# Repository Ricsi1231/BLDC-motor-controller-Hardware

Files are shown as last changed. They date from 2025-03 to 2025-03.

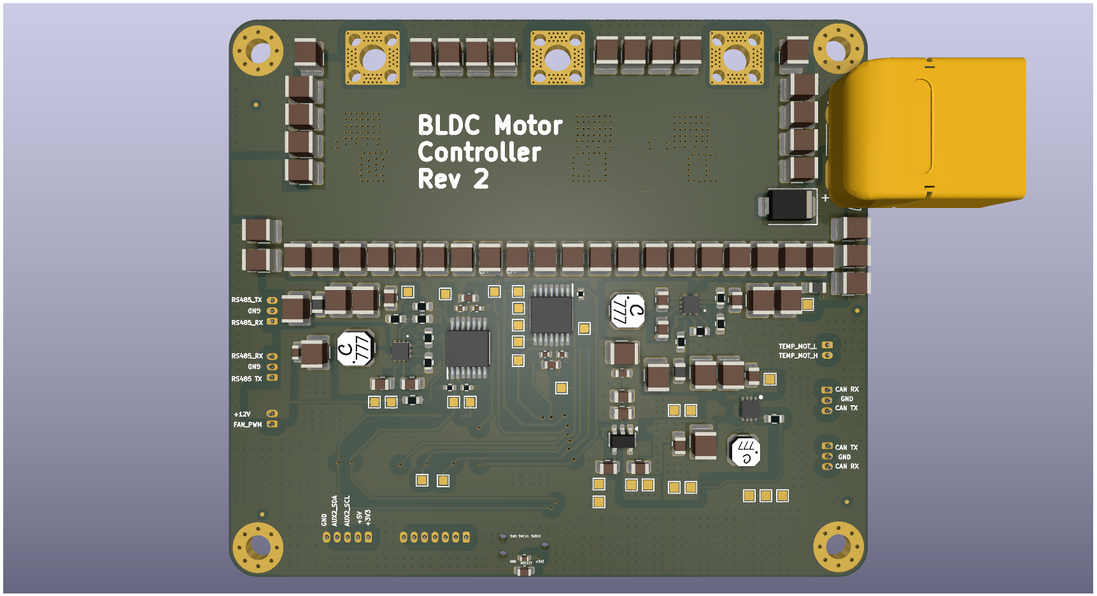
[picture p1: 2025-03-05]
BLDC motor controller/3D/BLDC motor controller - BOTTOM.png

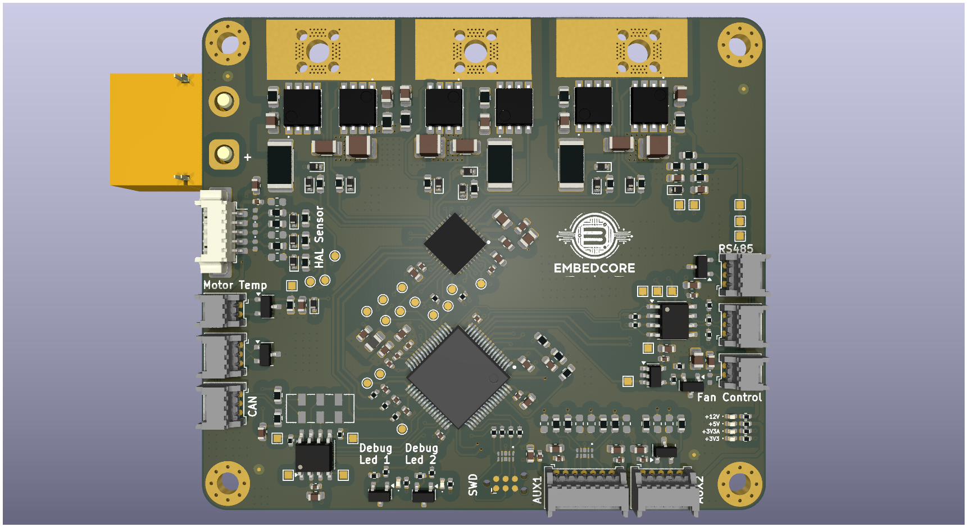
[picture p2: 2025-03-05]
BLDC motor controller/3D/BLDC motor controller - TOP.png

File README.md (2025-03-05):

## EmbedCore - BLDC Motor Controller

EmbedCore motor controller is a high-power brushless motor controller. It was specifically designed to be integrated in Autonomus Mobile Robot wheel actuators. Motor controller can be intagreted to other applications.
BLDC Motor Controller is also my final thesis work at Subotica Tech - College of Applied Sciences.

***

## SPECIFICATIONS

| Parameter | EmbedCore BLDC Controller V1.0 | 
| --- | --- |
| Voltage Input | 12-44V |
| Peak Electrical Power | TBD |
| Mass | TBD |
| Peak Phase Current | 100A |
| Communication | 5Mbps CAN-FD & RS485 |
| Cooling | 12V Fan |
| Positioning | 2x Onboard 14-bit Encoders |
| Control rate | 15-30kHz |
| PWM Switching Rate | 15-60kHz |
| MCU | STM32G474 |
| Dimensions | 67 x 76.5mm |

***

## DIRECTORY STRUCTURE

```
BLDC motor controller
├── 3D                             # 3D render pictures of the board
├── Datasheets                     # Main component datasheets
├── Specification                  # Specification description about the project
├── Documentation
│   |── Schematic                  # PDF Schematic
│   |── PCB                        # PCB Documentation in PDF
│   |── Computations               # Computations for the components
├── lib
    |── 3d_models                  # Component 3D models
    |── lib_fp                     # Footprint libraries
    |── lib_sym                    # Symbol libraries
├── Logos                          # EmbedCore logo
├── Manufacturing
│   |── Gerber                     # Gerbers files
│   |── BOOM                       # Bill of matirials
│   |── Component Postions         # Components positions for PCB assembly
│   |── Drill files                # Drill files for assembly
├── Templates                      # Title block templates
```

## FIRMWARE

Associated firmware is in [BLDC Motor Controller - Firmware](https://gitlab.com/autonomus-mobile-robot/firmware) repository.

## Lisence
The project is under Apache License 2.0 lisence.

## Support
If you need help about this board, you can reach me at this mail: embedcore7@gmail.com

***

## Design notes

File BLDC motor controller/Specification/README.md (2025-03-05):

# BLDC motor controller Specification

- BLDC Motor Controller Hardware General Description:
    - Operating voltage range: 12V - 44V.
    - Built-in bulk capacitance (200µF) for stable motor control and power supply. External precharge circuit required when connecting multiple boards.
    - Multiple voltage rails (3.3V, 3.3VA, 5V, 12V) for stable power supply.
    - Field-Oriented Control (FOC) for BLDC motor operation.
    - Current handling: 30A continuous, 100A peak.
    - Compatible with multiple BLDC motor types.
    - Supports RS485 and CAN communication protocols.
    - Hall sensors for closed-loop control.
    - Temperature monitoring for motor and MOSFETs.
    - Motor cooling capability.
    - Status indicator LEDs.
- Components:
    - **Buck converter**: LMR36506-Q1 - Converts 6S battery voltage to 5V and 12V, providing 600mA for fan and external peripherals.
    - **Buck converter**: TPS62172 - Converts 5V to 3.3V system voltage with 500mA output.
    - **LDO**: LP2992 - Converts 5V to 3.3V analog voltage with 250mA maximum output.
    - **MCU**: STM32G474RET6 - Low-power, high-performance MCU optimized for battery-powered applications.
    - **Motor controller**: DRV8353 - Advanced motor control IC with high current capability, controlling N-Channel MOSFETs.
    - **N-Channel MOSFETs**: TPW1R306PL,L1Q - Two MOSFETs per channel.
    - **NTC**: NTCS0402E3473FXT - Temperature sensor for MOSFETs.
    - **NTC**: TBD - Temperature sensor for motor.
    - **Encoders:** ASS5047P & AS5048B - Commutation and disambiguation encoders.
    - **CAN transceiver**: TCAN334GDCNT.
    - **RS485 transceiver**: SP3494.
    - **Cooling fan PWM driver**: DGD0216.
    - **Debug LEDs**: Two status indicators (red and green) for user feedback.
    - **Power connector**: 2× XT60.
    - **Input connectors**: One motor temperature sensing connector.
    - **Output connectors**: One 3-pin motor phase connector, one cooling connector.
    - **I/O connectors**: Two encoder connectors, two 3-pin CAN connectors, two 3-pin RS485 connectors, one SWD connector for debugging and firmware updates.
    
    ### STM32-based Firmware
    
    - Uses STM32 HAL library for efficient development.
    - Implemented in C++ to manage project complexity.
    - Class-based driver implementation for each device.
    - Separate classes for control algorithms including PID.
    - FreeRTOS implementation for task management.
    - Documented with block diagrams for architecture and functionality.
    - Layered architecture design.
    - Comprehensive error handling with device cross-monitoring.
    - Configurable settings with RS485 & CAN messaging support.
    - DMA and interrupt handling for I2C, SPI, UART, CAN, GPIO, and PWM.
    - Optimized memory management to prevent leaks.
    - Unit testing for all modules.

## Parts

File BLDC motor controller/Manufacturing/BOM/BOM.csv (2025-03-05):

Reference | Value | Datasheet | Footprint | Qty | DNP | Manufacturer | Manufacturer Part Number | Distributer Link
C501,C502,C503,C504,C505,C506,C507,C508,C509,C510,C511,C512,C513,C514,C515,C516,C517,C518,C519,C520,C521,C522,C523,C524,C525,C526,C527,C528,C529,C530,C531,C532,C533,C534,C535,C536,C537,C538,C539,C540,C541,C542,C1104,C1204,C1305 | 10u 100V X7R | https://product.tdk.com/system/files/dam/doc/product/capacitor/ceramic/mlcc/catalog/mlcc_commercial_midvoltage_en.pdf | Capacitor_SMD:C_1210_3225Metric | 45 |  | TDK | C3225X7R2A106K250AC | https://eu.mouser.com/
C601,C602,C603,C609,C610,C611,C617,C618 | 2u2 100V X7R | https://eu.mouser.com/datasheet/2/447/KEM_C1023_X7R_AUTO_SMD-3316698.pdf | Capacitor_SMD:C_1210_3225Metric | 8 |  | KEMET | C1210C225J1RACAUTO | https://eu.mouser.com/
C604,C606,C612,C614,C620 | 100n 100V X7R | https://eu.mouser.com/datasheet/2/40/X7RDielectric-2943470.pdf | Capacitor_SMD:C_0805_2012Metric | 5 |  | KYOCERA AVX | 08051C104JAZ2A | https://eu.mouser.com/
C605,C613 | 1u 50V X7R | https://eu.mouser.com/datasheet/2/40/KGM_X7R-3223212.pdf | Capacitor_SMD:C_0805_2012Metric | 2 |  | KYOCERA AVX | 08055C105JAT2A | https://eu.mouser.com/
C607,C615 | 22u 25V X7R | https://eu.mouser.com/datasheet/2/396/Tayio_Yuden_1102023_MS_mlcc_all_e-3081579.pdf | Capacitor_SMD:C_1210_3225Metric | 2 |  | TAIYO YUDEN | MSAST32MSB7226KPNB25 | https://eu.mouser.com/
C608,C616 | 100n 25V X7R | https://eu.mouser.com/datasheet/2/447/KEM_C1090_X7R_ESD-3316292.pdf | Capacitor_SMD:C_0603_1608Metric | 2 |  | KEMET | C0603C104J3RECAUTO7411 | https://eu.mouser.com/
C619 | 10u 25V X7R | https://eu.mouser.com/datasheet/2/281/1/GRM32DR71E106KA12_01A-1988306.pdf | Capacitor_SMD:C_1210_3225Metric | 1 |  | Murata Electronics | GRM32DR71E106KA12K | https://eu.mouser.com/
C622 | 22u 16V X7R | https://eu.mouser.com/datasheet/2/396/Tayio_Yuden_1102023_MS_mlcc_all_e-3081579.pdf | Capacitor_SMD:C_1210_3225Metric | 1 |  | TAIYO YUDEN | MSAST32MSB7226KPNB25 | https://eu.mouser.com/
C623,C702,C703 | 100n 25V X7R | https://eu.mouser.com/datasheet/2/40/X7RDielectric-2943470.pdf | Capacitor_SMD:C_0805_2012Metric | 3 |  | KYOCERA AVX | 08053C104KAZ2A | https://eu.mouser.com/
C701 | 2u2 16V X7R | https://eu.mouser.com/datasheet/2/447/KEM_C1023_X7R_AUTO_SMD-3316698.pdf | Capacitor_SMD:C_0805_2012Metric | 1 |  | KEMET | C0805C225K4RAC3123 | https://eu.mouser.com/
C704 | 4u7 16V X7R | https://eu.mouser.com/datasheet/2/447/KEM_C1002_X7R_SMD-3316098.pdf | Capacitor_SMD:C_0805_2012Metric | 1 |  | KEMET | C0805C475K4RAC7210 | https://eu.mouser.com/
C801 | 1u 16V X7R | https://eu.mouser.com/datasheet/2/396/mlcc06_hq_AUTO_e-1901145.pdf | Capacitor_SMD:C_0603_1608Metric | 1 |  | TAIYO YUDEN | EMK107B7105KA8T | https://eu.mouser.com/
C802,C807,C808,C810,C1007,C1601,C1604,C1701,C1703,C1801,C1901,C2001,C2003,C2009,C2011,C2015,C2024 | 4u7 16V X7R | https://eu.mouser.com/datasheet/2/281/1/GRM188Z71C475KE21_01A-1986016.pdf | Capacitor_SMD:C_0603_1608Metric | 17 |  | Murata Electronics | GRM188Z71C475KE21D | https://eu.mouser.com/
C803,C804,C805,C806,C809,C811,C1008,C1602,C1603,C1605,C1606,C1702,C1802,C1902,C2002,C2004,C2010,C2012,C2016,C2022 | 100n 16V X7R | https://product.tdk.com/system/files/dam/doc/product/capacitor/ceramic/mlcc/catalog/mlcc_commercial_general_en.pdf | Capacitor_SMD:C_0402_1005Metric | 20 |  | TDK | C1005X7R1C104K050BC | https://eu.mouser.com/
C1001,C2017 | 2u2 100V X7R | https://product.tdk.com/system/files/dam/doc/product/capacitor/ceramic/mlcc/catalog/mlcc_automotive_midvoltage_en.pdf | Capacitor_SMD:C_0805_2012Metric | 2 |  | TDK | CGA4J1X7R2A225K125AC | https://eu.mouser.com/
C1002,C1006,C1401,C1402,C1501,C2018,C2201 | 100n 100V X7R | https://eu.mouser.com/datasheet/2/40/AutoMLCCKAF-3218225.pdf | Capacitor_SMD:C_0603_1608Metric | 7 |  | KYOCERA AVX | KAF15BR72A104KT | https://eu.mouser.com/
C1005 | 1u 100V X7R | https://eu.mouser.com/datasheet/2/40/AutoMLCC-2952695.pdf | Capacitor_SMD:C_0805_2012Metric | 1 |  | KYOCERA AVX | 08051C105K4T2A | https://eu.mouser.com/
C1009 | 1u 6V3 X5R | https://eu.mouser.com/datasheet/2/585/Samsung_MLCC_1837944-1929650.pdf | Capacitor_SMD:C_0402_1005Metric | 1 |  | Samsung Electro-Mechanics | CL05B105KQ5QNWC | https://eu.mouser.com/
C1010 | 1u 16V X5R | https://eu.mouser.com/datasheet/2/396/mlcc06_hq_AUTO_e-1901145.pdf | Capacitor_SMD:C_0603_1608Metric | 1 |  | TAIYO YUDEN | EMK107B7105KA8T | https://eu.mouser.com/
C1011,C1012,C1013 | 1n 16V X7R | https://eu.mouser.com/datasheet/2/281/1/GRM155R71C103KA01_01A-1983887.pdf | Capacitor_SMD:C_0402_1005Metric | 3 |  | Murata Electronics | GRM155R71C103KA01J | https://eu.mouser.com/
C1101,C1102,C1201,C1202,C1301,C1302 | 22n 100V X7R | https://eu.mouser.com/datasheet/2/40/AutoMLCCKAM-3216307.pdf | Capacitor_SMD:C_0805_2012Metric | 6 |  | KYOCERA AVX | KAM21BR72A223KM | https://eu.mouser.com/
C1103,C1203,C1304 | 100n 100V X7R | https://www.we-online.com/components/products/datasheet/885382208006.pdf | Capacitor_SMD:C_1206_3216Metric | 3 |  | Wurth Elektronik | 885382208006 | https://eu.mouser.com/
D401 | SMBJ51CA-E3/52 | https://www.vishay.com/docs/88392/smbj.pdf | Diode_SMD:D_SMB | 1 |  | Vishay General Semiconductor | SMBJ51CA-E3/52 | https://eu.mouser.com/
D1101,D1102,D1103,D1201,D1202,D1203,D1301,D1302,D1303,D1401,D1402,D1403,D1404,D1405 | BAT41KFILM | https://eu.mouser.com/datasheet/2/389/bat41-1848934.pdf | Diode_SMD:D_SOD-523 | 14 |  | STMicroelectronics | BAT41KFILM | https://eu.mouser.com/
D2001,D2004 | ESDR0524SMUTAG | https://www.st.com/resource/en/datasheet/esda5v3sc6.pdf | ESDR0524SMUTAG:ESDR0524SMUTAG | 2 |  | onsemi | ESDR0524SMUTAG | https://eu.mouser.com/
D2002,D2003,D2005,D2006 | DF3A5.6LFU,LF | https://www.st.com/resource/en/datasheet/esdal.pdf | Package_TO_SOT_SMD:SOT-23-3 | 4 |  | Toshiba | DF3A5.6LFU,LF | https://eu.mouser.com/
D2007 | CG0402MLC-3.3LG | https://eu.mouser.com/datasheet/2/54/MLC-777442.pdf | Diode_SMD:D_0402_1005Metric | 1 |  | Bourns | CG0402MLC-3.3LG | https://eu.mouser.com/
D2009,D2010,D2011 | CG0402MLC-12G | https://eu.mouser.com/datasheet/2/54/MLC-777442.pdf | Diode_SMD:D_0402_1005Metric | 3 |  | Bourns | CG0402MLC-12LG | https://eu.mouser.com/
D2101,D2103 | GREEN | https://eu.mouser.com/datasheet/2/917/stanley_led_2018_02-1504930.pdf | LED_SMD:LED_0402_1005Metric | 2 |  | Stanley Electric | FHD1105P-TR | https://eu.mouser.com/
D2102 | RED | https://eu.mouser.com/datasheet/2/917/downloaddatafile-3318113.pdf | LED_SMD:LED_0402_1005Metric | 1 |  | Stanley Electric | FHR1105P-TR | https://eu.mouser.com/
D2104 | YELLOW | https://eu.mouser.com/datasheet/2/917/stanley_led_2018_02-1504930.pdf | LED_SMD:LED_0402_1005Metric | 1 |  | Stanley Electric | FHY1105P-TR | https://eu.mouser.com/
D2105 | BLUE | https://www.we-online.com/components/products/datasheet/150040BS73220.pdf | LED_SMD:LED_0402_1005Metric | 1 |  | Wurth Elektronik | 150040BS73220 | https://eu.mouser.com/
D2106 | ORAGNGE | https://www.we-online.com/components/products/datasheet/150040BS73220.pdf | LED_SMD:LED_0402_1005Metric | 1 |  | Bivar | SM0402OC | https://eu.mouser.com/
F603,FB601,FB602,FB801 | 1k @100MHz | https://eu.mouser.com/datasheet/2/3/ACML-0805H-43744.pdf | Inductor_SMD:L_0805_2012Metric | 4 |  | ABRACON | ACML-0805H-102-T | https://eu.mouser.com/
J2001 | Conn_01x07 | https://www.molex.com/en-us/products/part-detail/530480710?display=pdf | Connector_Molex:Molex_PicoBlade_53048-0710_1x07_P1.25mm_Horizontal | 1 |  | Molex | 53048-0710 | https://eu.mouser.com/
J2004,J2005,J2008,J2009 | Conn_01x03 | https://www.molex.com/en-us/products/part-detail/530480310?display=pdf | Connector_Molex:Molex_PicoBlade_53048-0310_1x03_P1.25mm_Horizontal | 4 |  | Molex | 53048-0310 | https://eu.mouser.com/
J2011,J2012 | Conn_01x02 | https://www.molex.com/en-us/products/part-detail/530480210?display=pdf | Connector_Molex:Molex_PicoBlade_53048-0210_1x02_P1.25mm_Horizontal | 2 |  | Molex | 53048-0210 | https://eu.mouser.com/
J2202 | Conn_01x05 | https://www.molex.com/en-us/products/part-detail/530480510?display=pdf | Connector_Molex:Molex_PicoBlade_53048-0510_1x05_P1.25mm_Horizontal | 1 |  | Molex | 53048-0510 | https://eu.mouser.com/
J2203 | Conn_01x05 | https://www.molex.com/en-us/products/part-detail/532610571?display=pdf | Connector_Molex:Molex_PicoBlade_53261-0571_1x05-1MP_P1.25mm_Horizontal | 1 |  | Molex | 53261-0571 | https://eu.mouser.com/
L601,L602 | 22.0u | https://eu.mouser.com/datasheet/2/597/lps4018-270702.pdf | inductor:L_Coilcraft_LPS4018 | 2 |  | Coilcraft | LPS4018-223MRC | https://eu.mouser.com/
L603 | 2.0u2 | https://eu.mouser.com/datasheet/2/597/lps3314-1301810.pdf | inductor:L_Coilcraft_LPS3314 | 1 |  | Coilcraft | LPS3314-222MRC | https://eu.mouser.com/
Q1101,Q1102,Q1201,Q1202,Q1301,Q1302 | TPW1R306PL,L1Q | https://ngspice.sourceforge.io/docs/ngspice-html-manual/manual.xhtml#cha_MOSFETs | SOP_ADVANCE:SOP_ADVANCE | 6 |  | Toshiba | TPW1R306PL,L1Q | https://www.digikey.com/
Q1901,Q2101,Q2102 | PMV90ENER | https://ngspice.sourceforge.io/docs/ngspice-html-manual/manual.xhtml#cha_MOSFETs | Package_TO_SOT_SMD:SOT-23 | 3 |  | Nexperia USA Inc. | PMV90ENER | https://www.digikey.com/
R601,R605 | 14000.0% | https://industrial.panasonic.com/cdbs/www-data/pdf/RDO0000/AOA0000C331.pdf | Resistor_SMD:R_0603_1608Metric | 2 |  | Panasonic | ERJ-PA3F1403V | https://eu.mouser.com/
R602,R604,R606,R608,R611,R901,R1402,R1403,R1903,R1904,R1905 | 1000.0% | https://industrial.panasonic.com/cdbs/www-data/pdf/RDO0000/AOA0000C331.pdf | Resistor_SMD:R_0603_1608Metric | 11 |  | Panasonic | ERJ-PA3F1002V | https://eu.mouser.com/
R603,R607 | 0.00R | https://www.mouser.com/catalog/specsheets/Panasonic_01052021_Resistor_Thick_FIlm_HI_Temp_ERJ_Hxx%20Series.pdf | Resistor_SMD:R_0603_1608Metric | 2 |  | Panasonic | ERJ-H3G0R00V | https://eu.mouser.com/
R609,R1501,R2201 | 10000.0% | ~https://www.mouser.com/catalog/specsheets/Panasonic_Resistors%20Thick%20Film%20Anti%20Sulf%20Anti%20Surge%20(ERJ-UP3%20Series).pdf | Resistor_SMD:R_0603_1608Metric | 3 |  | Panasonic | ERJ-UP3F1003V | https://eu.mouser.com/
R610 | 08-31-00 | https://www.mouser.com/catalog/specsheets/Panasonic_Resistors%20Thick%20Film%20Anti%20Sulf%20Anti%20Surge%20(ERJ-UP3%20Series).pdf | Resistor_SMD:R_0603_1608Metric | 1 |  | Panasonic | ERJ-UP3F9531V | https://eu.mouser.com/
R1001,R1002,R1003,R2008,R2009,R2011,R20010 | 2200.0% | https://industrial.panasonic.com/cdbs/www-data/pdf/RDO0000/AOA0000C331.pdf | Resistor_SMD:R_0402_1005Metric | 7 |  | Panasonic | ERJ-PA2F22R0X | https://eu.mouser.com/
R1004,R1005,R1601,R1602,R1603,R1701,R1702,R1801,R1802,R1902,R2101,R2102,R2103,R2104,R2105,R2106,R2107,R2108,R2109,R2110 | 1000.0% | https://industrial.panasonic.com/cdbs/www-data/pdf/RDO0000/AOA0000C331.pdf | Resistor_SMD:R_0402_1005Metric | 20 |  | Panasonic | ERJ-PA2F1002X | https://eu.mouser.com/
R1101,R1102,R1201,R1202,R1301,R1302 | 06-30-00 | https://industrial.panasonic.com/cdbs/www-data/pdf/RDP0000/AOA0000C334.pdf | Resistor_SMD:R_0603_1608Metric | 6 |  | Panasonic | ERJ-U03F7R50V | https://eu.mouser.com/
R1103,R1203,R1303 | 0m5 1% 2W | https://eu.mouser.com/datasheet/2/447/PYu_PA0100_2512_51_RoHS_2-2604383.pdf | Resistor_SMD:R_2512_6332Metric | 3 |  | YAGEO | PA2512FKE7W0R005E | https://eu.mouser.com/
R1104,R1105,R1204,R1205,R1304,R1305 | 2200.0% | https://industrial.panasonic.com/cdbs/www-data/pdf/RDA0000/AOA0000C304.pdf | Resistor_SMD:R_0805_2012Metric | 6 |  | Panasonic | ERJ-6ENF22R0V | https://eu.mouser.com/
R1502 | 03-31-00 | https://www.mouser.com/catalog/specsheets/Panasonic_Resistors%20Thick%20Film%20Anti%20Sulf%20Anti%20Surge%20(ERJ-UP3%20Series).pdf | Resistor_SMD:R_0603_1608Metric | 1 |  | Panasonic | ERJ-UP3F4701V | https://eu.mouser.com/
R1703,R1705 | 39000.0% | https://industrial.panasonic.com/cdbs/www-data/pdf/RDO0000/AOA0000C331.pdf | Resistor_SMD:R_0402_1005Metric | 2 |  | Panasonic | ERJ-PA2D3900X | https://eu.mouser.com/
R1704 | 120.00R | https://industrial.panasonic.com/cdbs/www-data/pdf/RDO0000/AOA0000C331.pdf | Resistor_SMD:R_0402_1005Metric | 1 |  | Panasonic | ERJ-PA2D1200X | https://eu.mouser.com/
R1803,R1804 | 60R4 1% 1/4W | https://www.mouser.com/catalog/specsheets/Panasonic_Resistors%20Thick%20Film%20Anti%20Sulf%20Anti%20Surge%20(ERJ-UP3%20Series).pdf | Resistor_SMD:R_0603_1608Metric | 2 |  | Panasonic | ERJ-UP3F60R4V | https://eu.mouser.com/
R1901 | 1000.0% | https://industrial.panasonic.com/cdbs/www-data/pdf/RDO0000/AOA0000C331.pdf | Resistor_SMD:R_0402_1005Metric | 1 |  | Panasonic | ERJ-PA2D10R0X | https://eu.mouser.com/
R2001,R2002,R2003,R2004,R2006,R2007,R2010,R2012,R2013 | 10000.0% | https://www.mouser.com/catalog/specsheets/Panasonic_Resistors%20Thick%20Film%20Anti%20Sulf%20Anti%20Surge%20(ERJ-UP3%20Series).pdf | Resistor_SMD:R_0603_1608Metric | 9 |  | Panasonic | ERJ-UP3F1000V | https://eu.mouser.com/
SW2001 | CAS-220TA | https://eu.mouser.com/datasheet/2/972/cas-1628136.pdf | Button_Switch_SMD:SW_DPDT_CK_JS202011JCQN | 1 |  | Nidec Components | CAS-220TA | https://eu.mouser.com/
TH1401 | 47k 1% NTC | https://eu.mouser.com/datasheet/2/281/NCU18WB473D6SRB-1108692.pdf | Resistor_SMD:R_0603_1608Metric | 1 |  | Murata Electronics | NCU18WB473D6SRB | https://eu.mouser.com/
U601 | LMR36506MSC5RPERQ1 | https://www.ti.com/lit/ds/symlink/lmr36506-q1.pdf?ts=1740816467259 | LMR36506MSC5RPERQ1:LMR36506MSC5RPERQ1 | 1 |  | Texas Instruments | LMR36506MSC5RPERQ1 | https://eu.mouser.com/
U602 | LMR36506MSCQRPERQ1 | https://www.ti.com/lit/ds/symlink/lmr36506-q1.pdf?ts=1729963450516 | LMR36506MSC5RPERQ1:LMR36506MSC5RPERQ1 | 1 |  | Texas Instruments | LMR36506MSCQRPERQ1 | https://eu.mouser.com/
U603 | TPS62172 | https://www.ti.com/lit/ds/symlink/tps62172-q1.pdf?ts=1740816634162 | SON50P200X200X80-9N:SON50P200X200X80-9N | 1 |  | Texas Instruments | TPS62172QDSGRQ1 | https://eu.mouser.com/
U701 | LP2992 | https://www.ti.com/lit/ds/symlink/lp2992.pdf?ts=1740738733951 | Package_TO_SOT_SMD:SOT-23-5 | 1 |  | Texas Instruments | LP2992AILDX-3.3/NOPB | https://eu.mouser.com/
U801_901 | STM32G474RET6 | https://eu.mouser.com/datasheet/2/389/stm32g474cb-1600828.pdf | QFP50P1200X1200X160-64N:QFP50P1200X1200X160-64N | 1 |  | STMicroelectronics | STM32G474RET6 | https://eu.mouser.com/
U1001 | DRV8353FS | https://www.ti.com/lit/ds/symlink/drv8353f.pdf?ts=1740784220782 | QFN50P600X600X80-41N-D:QFN50P600X600X80-41N-D | 1 |  | Texas Instruments | DRV8353FSRTAR | https://eu.mouser.com/
U1601 | ASS5047P | https://eu.mouser.com/datasheet/2/588/asset_pdf_25493104-3419339.pdf | SOP65P640X120-14N:SOP65P640X120-14N | 1 |  | ams OSRAM | AS5047P-ATSM | https://eu.mouser.com/
U1602 | AS5048B | https://eu.mouser.com/datasheet/2/588/asset_pdf_25493108-3418798.pdf | SOP65P640X120-14N:SOP65P640X120-14N | 1 |  | ams OSRAM | AS5048B-HTSP | https://eu.mouser.com/
U1701 | SP3494 | https://www.maxlinear.com/ds/sp3494.pdf | Package_SO:SOIC-8_3.9x4.9mm_P1.27mm | 1 |  | MaxLinear | SP3494EN-L | https://eu.mouser.com/
U1801 | TCAN330 | http://www.ti.com/lit/ds/symlink/tcan337.pdf | Package_SO:SOIC-8_3.9x4.9mm_P1.27mm | 1 |  | Texas Instruments | TCAN330GDR | https://eu.mouser.com/
U1901 | DGD0216 | https://www.diodes.com/datasheet/download/DGD0215%2F0216.pdf | Package_TO_SOT_SMD:SOT-23-5 | 1 |  | Diodes Incorporated | DGD0216WT-7 | https://eu.mouser.com/

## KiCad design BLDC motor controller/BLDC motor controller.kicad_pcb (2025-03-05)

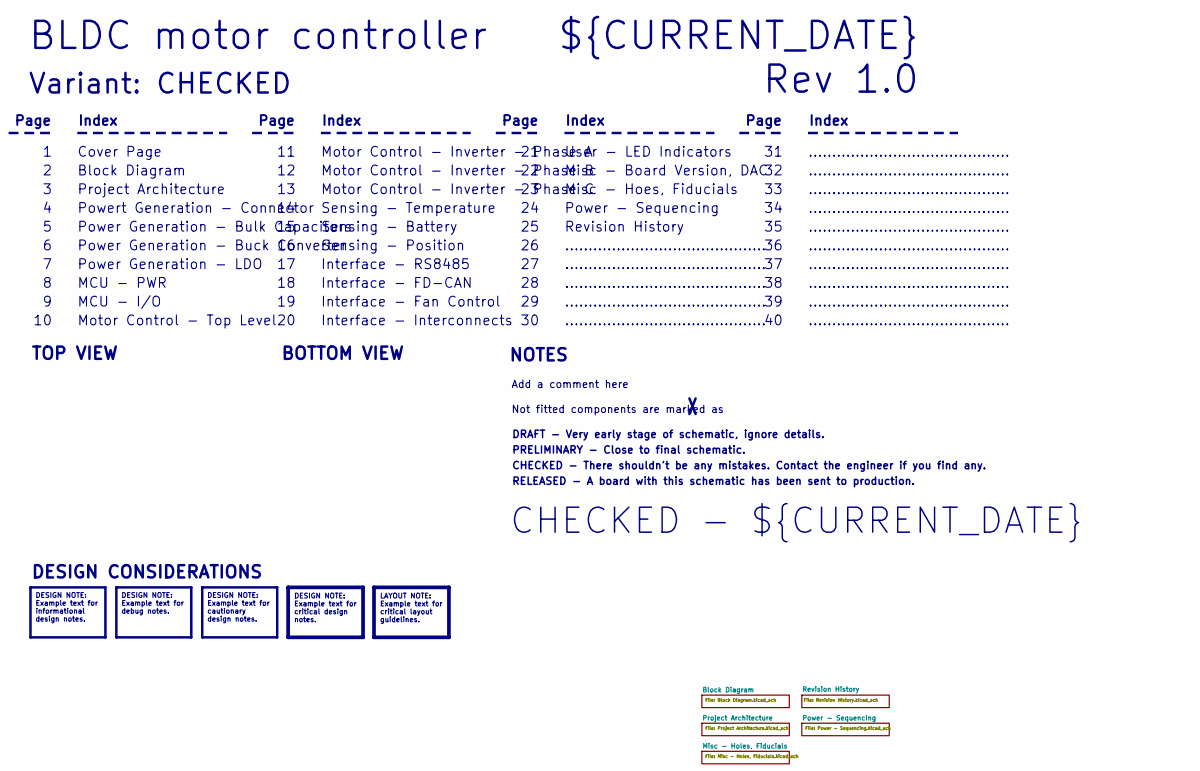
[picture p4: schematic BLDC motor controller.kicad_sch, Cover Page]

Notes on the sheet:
BOTTOM VIEW
Misc - Hoes, Fiducials
RELEASED - A board with this schematic has been sent to production.
Page
TOP VIEW
Motor Control - Top Level
MCU - I/O
MCU - PWR
Sensing - Position
Not fitted components are marked as
...........................................
Index
Motor Control - Inverter - Phase C
PRELIMINARY - Close to final schematic.
CHECKED - ${CURRENT_DATE}
Powert Generation - Connector
${CURRENT_DATE}
Variant: CHECKED
Rev 1.0
Power - Sequencing
Misc - Board Version, DAC
Power Generation - Bulk Capacitors
Interface - Fan Control
Motor Control - Inverter - Phase A
Interface - RS8485
Sensing - Battery
BLDC motor controller
DRAFT - Very early stage of schematic, ignore details.
Sensing - Temperature
Power Generation - Buck Converter
Block Diagram
Revision History
Add a comment here
Interface - FD-CAN
Interface - Interconnects
Cover Page
NOTES
Motor Control - Inverter - Phase B
Project Architecture
CHECKED - There shouldn't be any mistakes. Contact the engineer if you find any.

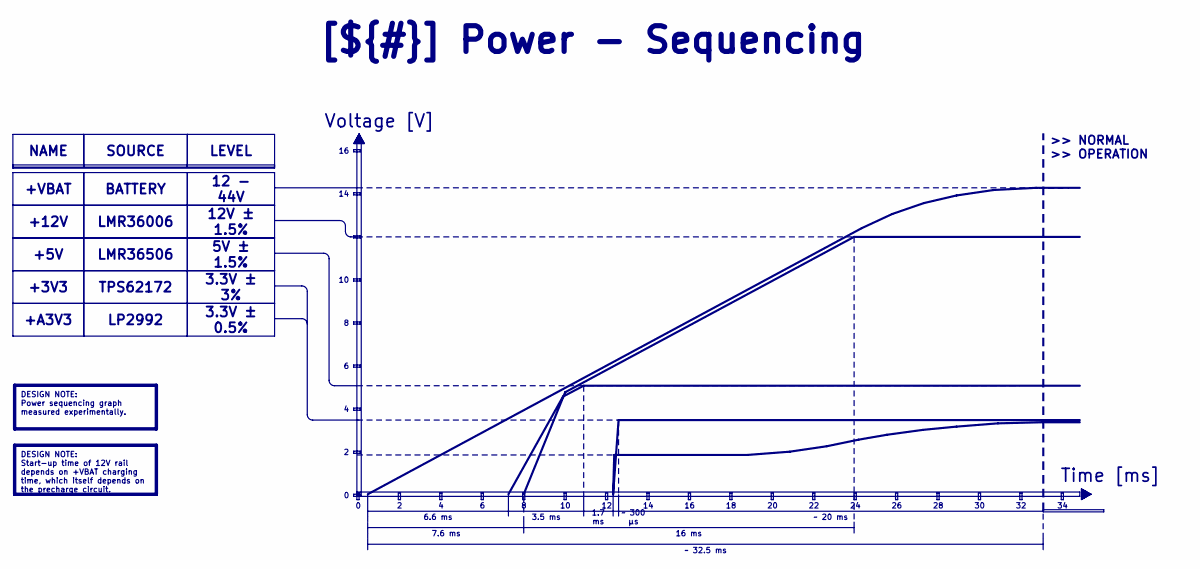
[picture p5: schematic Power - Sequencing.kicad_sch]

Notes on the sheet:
Time [ms]
Voltage [V]
>> NORMAL >> OPERATION
~ 20 ms
+12V
3.3V ± 0.5%
LMR36006
16 ms
12V ± 1.5%
+5V
LP2992
TPS62172
6.6 ms
LMR36506
NAME
DESIGN NOTE: Start-up time of 12V rail depends on +VBAT charging time, which itself depends on the precharge circuit.
12 - 44V
DESIGN NOTE: Power sequencing graph measured experimentally.
SOURCE
[${#}] ${TITLE}
LEVEL
+VBAT
+A3V3
BATTERY
5V ± 1.5%
+3V3
7.6 ms
~ 300 μs
3.3V ± 3%
3.5 ms
1.7 ms
~ 32.5 ms

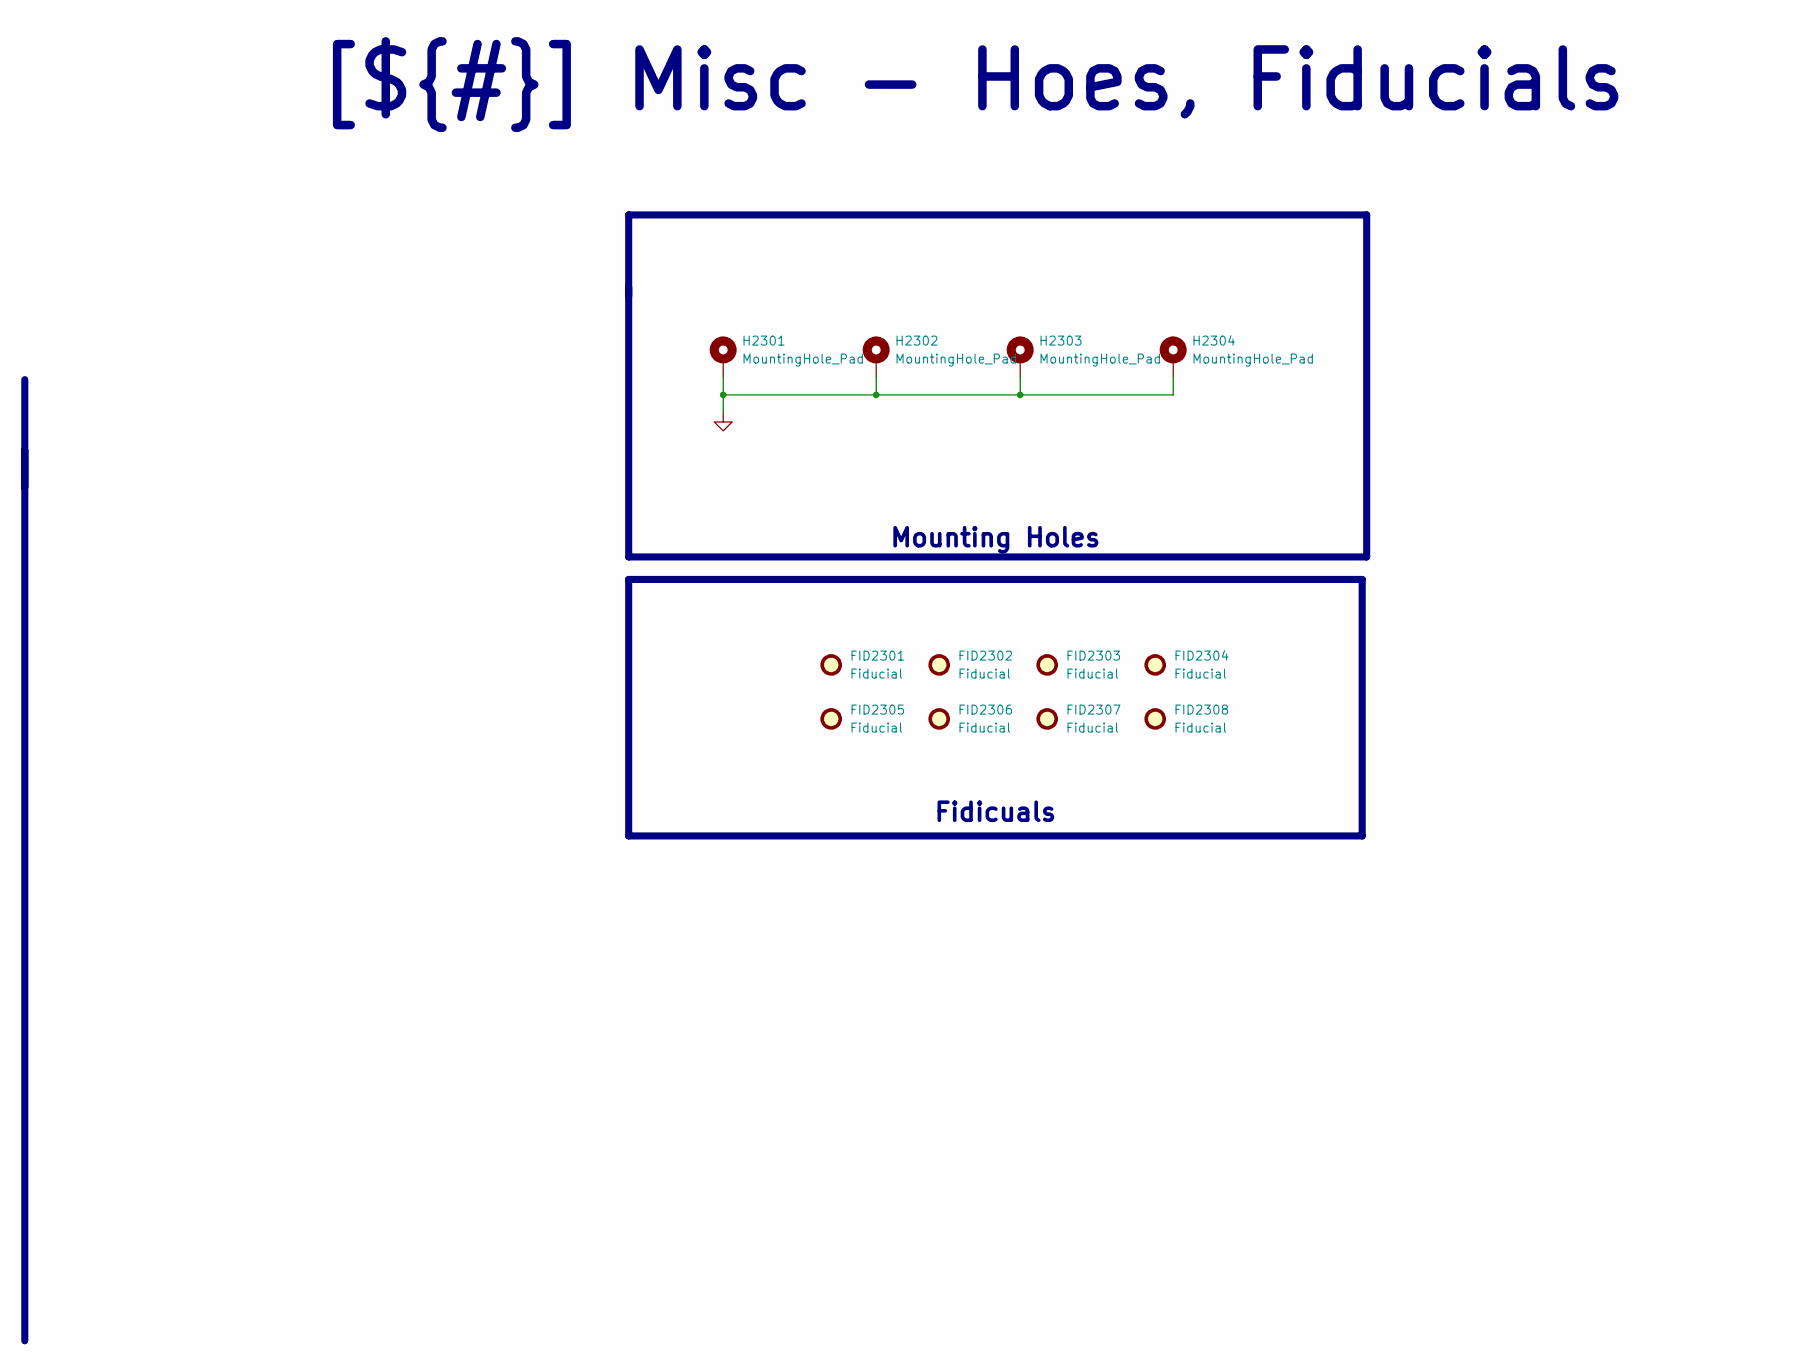
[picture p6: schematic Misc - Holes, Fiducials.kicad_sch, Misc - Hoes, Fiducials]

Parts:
FID2301, FID2302, FID2303, FID2304, FID2305, FID2306, FID2307, FID2308: Fiducial; Fiducial_0.5mm_Mask1.5mm
H2301, H2302, H2303, H2304: MountingHole_Pad; MountingHole_3mm_Pad_Via

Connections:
GND: H2301.1, H2302.1, H2303.1, H2304.1; also elsewhere on the board

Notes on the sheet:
Fidicuals
[${#}] ${TITLE}
Mounting Holes

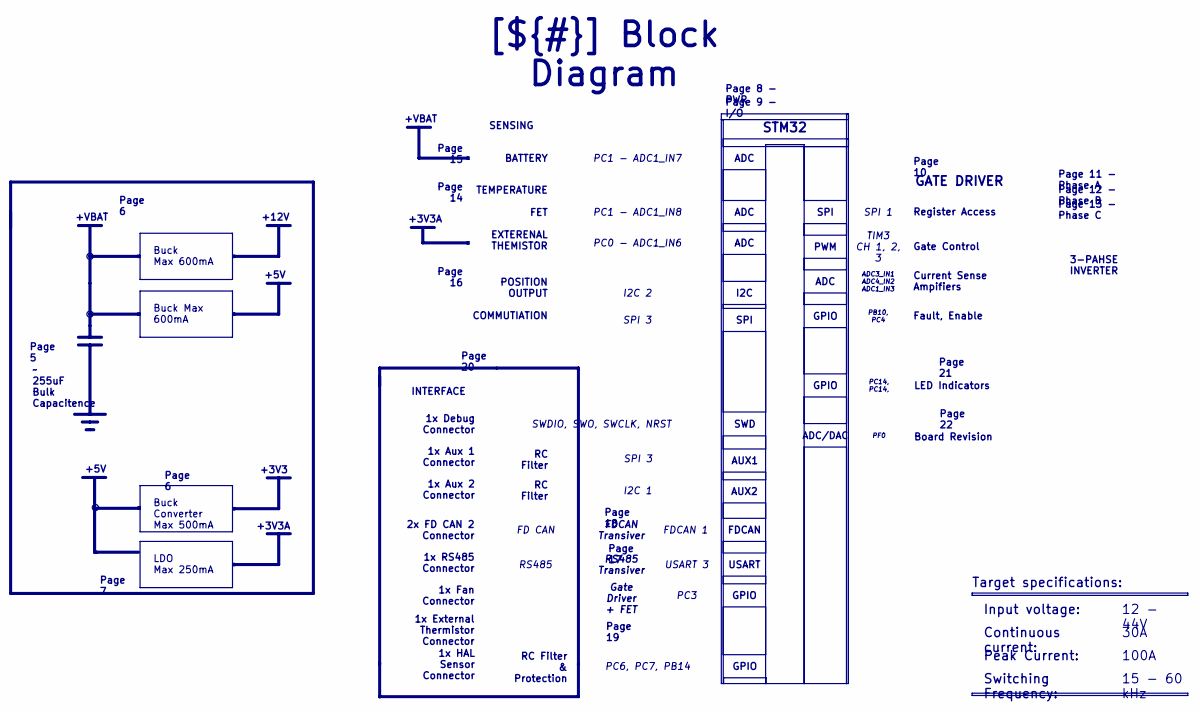
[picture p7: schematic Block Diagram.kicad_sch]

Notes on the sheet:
+3V3
+12V
+5V
+3V3A
+VBAT
1x Aux 2 Connector
LED Indicators
1x RS485 Connector
Page 21
Peak Current:
Buck Max 600mA
ADC
1x Aux 1 Connector
Page 19
SWDIO, SWO, SWCLK, NRST
USART
~ 255uF Bulk Capacitence
1x Debug Connector
RS485
Continuous current:
RS485 Transiver
PC1 - ADC1_IN8
2x FD CAN 2 Connector
STM32
SPI 3
Page 12 - Phase B
1x External Thermistor Connector
Page 10
SPI 1
Input voltage:
PC1 - ADC1_IN7
15 - 60 kHz
30A
AUX2
POSITION OUTPUT COMMUTIATION
ADC3_IN1 ADC4_IN2 ADC1_IN3
I2C 2
FD CAN
GPIO
GATE DRIVER

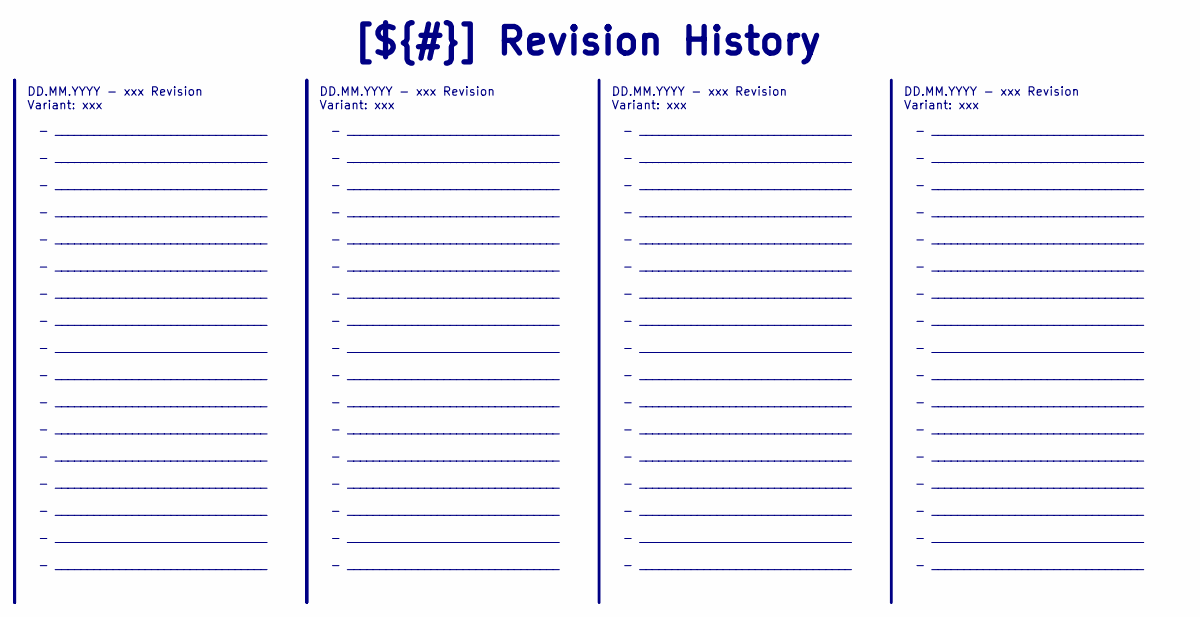
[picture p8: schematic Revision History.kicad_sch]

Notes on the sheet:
- _________________________________ - _________________________________ - _________________________________ - _________________________________ - _________________________________ - _________________________________ - _________________________________ - _________________________________ - _________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
DD.MM.YYYY - xxx Revision Variant: xxx
[${#}] ${TITLE}

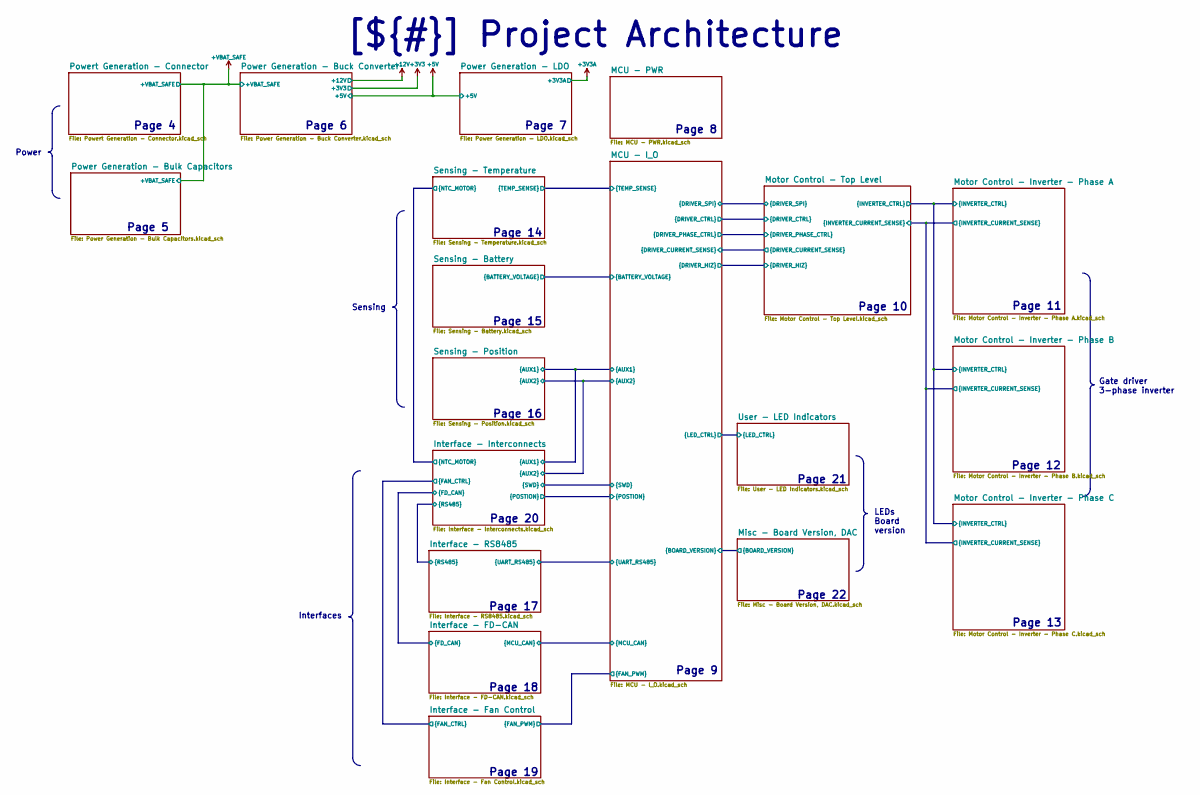
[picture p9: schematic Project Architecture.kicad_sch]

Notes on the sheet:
Page 13
Page 16
Page 19
Page 8
Page 22
Page 9
Page 5
Page 11
Page 21
Page 12
Page 10
Page 14
Page 7
Page 4
Page 6
Page 17
Page 15
Page 18
Page 20
Sensing
Interfaces
Gate driver 3-phase inverter
LEDs Board version
[${#}] ${TITLE}
Power

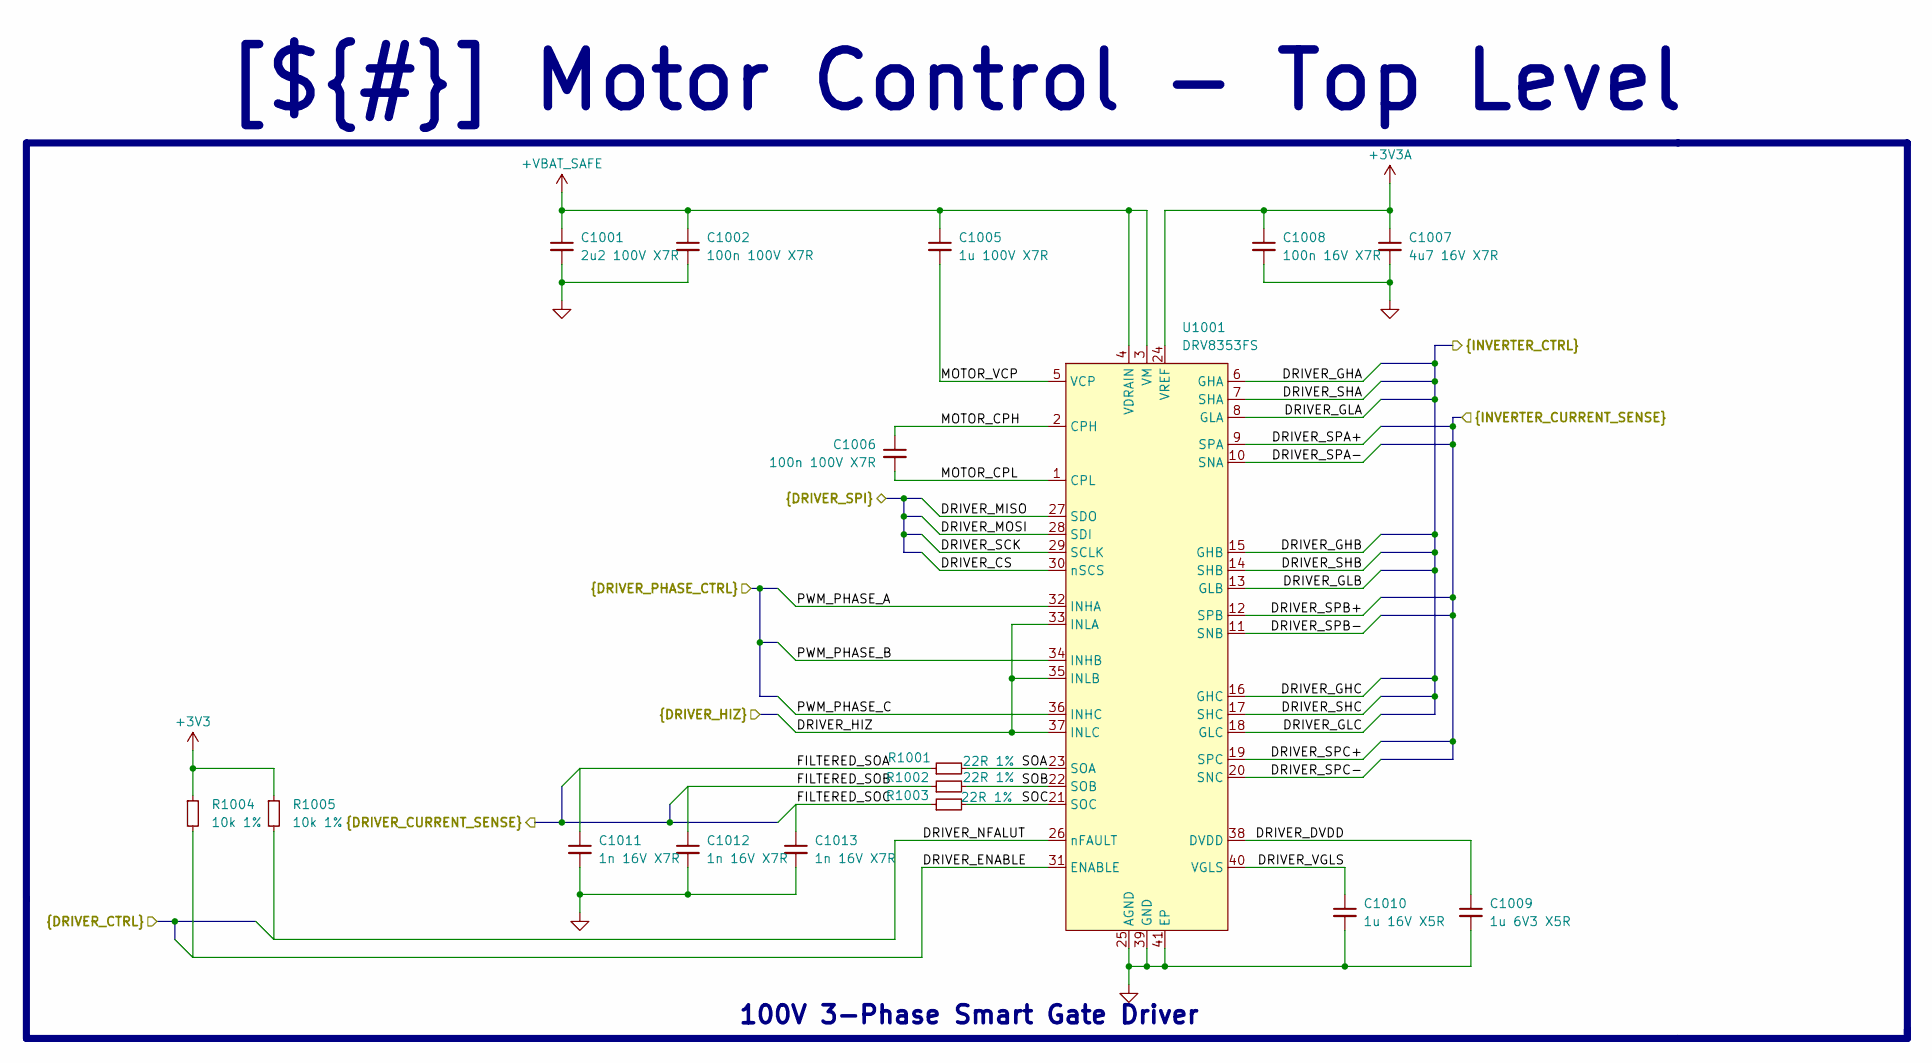
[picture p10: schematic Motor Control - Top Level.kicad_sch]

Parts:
C1001: 2u2 100V X7R; C_0805_2012Metric; Manufacturer Part Number CGA4J1X7R2A225K125AC
C1002, C1006: 100n 100V X7R; C_0603_1608Metric; Manufacturer Part Number KAF15BR72A104KT
C1005: 1u 100V X7R; C_0805_2012Metric; Manufacturer Part Number 08051C105K4T2A
C1007: 4u7 16V X7R; C_0603_1608Metric; Manufacturer Part Number GRM188Z71C475KE21D
C1008: 100n 16V X7R; C_0402_1005Metric; Manufacturer Part Number C1005X7R1C104K050BC
C1009: 1u 6V3 X5R; C_0402_1005Metric; Manufacturer Part Number CL05B105KQ5QNWC
C1010: 1u 16V X5R; C_0603_1608Metric; Manufacturer Part Number EMK107B7105KA8T
C1011, C1012, C1013: 1n 16V X7R; C_0402_1005Metric; Manufacturer Part Number GRM155R71C103KA01J
R1001, R1002, R1003: 22R 1%; R_0402_1005Metric; Manufacturer Part Number ERJ-PA2F22R0X
R1004, R1005: 10k 1%; R_0402_1005Metric; Manufacturer Part Number ERJ-PA2F1002X
U1001: DRV8353FS; QFN50P600X600X80-41N-D; Manufacturer Part Number DRV8353FSRTAR

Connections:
+3V3: R1004.1, R1005.1; also elsewhere on the board
+3V3A: C1007.1, C1008.1, U1001.24 (VREF); also elsewhere on the board
+VBAT_SAFE: C1001.1, C1002.1, C1005.1, U1001.3 (VM), U1001.4 (VDRAIN); also elsewhere on the board
/Project Architecture/MCU - I_O/DRIVER_CS: U1001.30 (nSCS); also elsewhere on the board
/Project Architecture/MCU - I_O/DRIVER_ENABLE: R1004.2, U1001.31 (ENABLE); also elsewhere on the board
/Project Architecture/MCU - I_O/DRIVER_HIZ: U1001.33 (INLA), U1001.35 (INLB), U1001.37 (INLC); also elsewhere on the board
/Project Architecture/MCU - I_O/DRIVER_MISO: U1001.27 (SDO); also elsewhere on the board
/Project Architecture/MCU - I_O/DRIVER_MOSI: U1001.28 (SDI); also elsewhere on the board
/Project Architecture/MCU - I_O/DRIVER_NFALUT: R1005.2, U1001.26 (nFAULT); also elsewhere on the board
/Project Architecture/MCU - I_O/DRIVER_SCK: U1001.29 (SCLK); also elsewhere on the board
/Project Architecture/MCU - I_O/FILTERED_SOA: C1011.1, R1001.1; also elsewhere on the board
/Project Architecture/MCU - I_O/FILTERED_SOB: C1012.1, R1002.1; also elsewhere on the board
/Project Architecture/MCU - I_O/FILTERED_SOC: C1013.1, R1003.1; also elsewhere on the board
/Project Architecture/MCU - I_O/PWM_PHASE_A: U1001.32 (INHA); also elsewhere on the board
/Project Architecture/MCU - I_O/PWM_PHASE_B: U1001.34 (INHB); also elsewhere on the board
/Project Architecture/MCU - I_O/PWM_PHASE_C: U1001.36 (INHC); also elsewhere on the board
/Project Architecture/Motor Control - Inverter - Phase A/DRIVER_GHA: U1001.6 (GHA); also elsewhere on the board
/Project Architecture/Motor Control - Inverter - Phase A/DRIVER_GHB: U1001.15 (GHB); also elsewhere on the board
/Project Architecture/Motor Control - Inverter - Phase A/DRIVER_GHC: U1001.16 (GHC); also elsewhere on the board
/Project Architecture/Motor Control - Inverter - Phase A/DRIVER_GLA: U1001.8 (GLA); also elsewhere on the board
/Project Architecture/Motor Control - Inverter - Phase A/DRIVER_GLB: U1001.13 (GLB); also elsewhere on the board
/Project Architecture/Motor Control - Inverter - Phase A/DRIVER_GLC: U1001.18 (GLC); also elsewhere on the board
/Project Architecture/Motor Control - Inverter - Phase A/DRIVER_SHA: U1001.7 (SHA); also elsewhere on the board
/Project Architecture/Motor Control - Inverter - Phase A/DRIVER_SHB: U1001.14 (SHB); also elsewhere on the board
/Project Architecture/Motor Control - Inverter - Phase A/DRIVER_SHC: U1001.17 (SHC); also elsewhere on the board
/Project Architecture/Motor Control - Inverter - Phase A/DRIVER_SPA+: U1001.9 (SPA); also elsewhere on the board
/Project Architecture/Motor Control - Inverter - Phase A/DRIVER_SPA-: U1001.10 (SNA); also elsewhere on the board
/Project Architecture/Motor Control - Inverter - Phase A/DRIVER_SPB+: U1001.12 (SPB); also elsewhere on the board
/Project Architecture/Motor Control - Inverter - Phase A/DRIVER_SPB-: U1001.11 (SNB); also elsewhere on the board
/Project Architecture/Motor Control - Inverter - Phase A/DRIVER_SPC+: U1001.19 (SPC); also elsewhere on the board
/Project Architecture/Motor Control - Inverter - Phase A/DRIVER_SPC-: U1001.20 (SNC); also elsewhere on the board
/Project Architecture/Motor Control - Top Level/DRIVER_DVDD: C1009.1, U1001.38 (DVDD)
/Project Architecture/Motor Control - Top Level/DRIVER_VGLS: C1010.1, U1001.40 (VGLS)
/Project Architecture/Motor Control - Top Level/MOTOR_CPH: C1006.1, U1001.2 (CPH)
/Project Architecture/Motor Control - Top Level/MOTOR_CPL: C1006.2, U1001.1 (CPL)
/Project Architecture/Motor Control - Top Level/MOTOR_VCP: C1005.2, U1001.5 (VCP)
/Project Architecture/Motor Control - Top Level/SOA: R1001.2, U1001.23 (SOA)
/Project Architecture/Motor Control - Top Level/SOB: R1002.2, U1001.22 (SOB)
/Project Architecture/Motor Control - Top Level/SOC: R1003.2, U1001.21 (SOC)
GND: C1001.2, C1002.2, C1007.2, C1008.2, C1009.2, C1010.2, C1011.2, C1012.2, C1013.2, U1001.25 (AGND), U1001.39 (GND), U1001.41 (EP); also elsewhere on the board

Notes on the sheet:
[${#}] Motor Control - Top Level
100V 3-Phase Smart Gate Driver

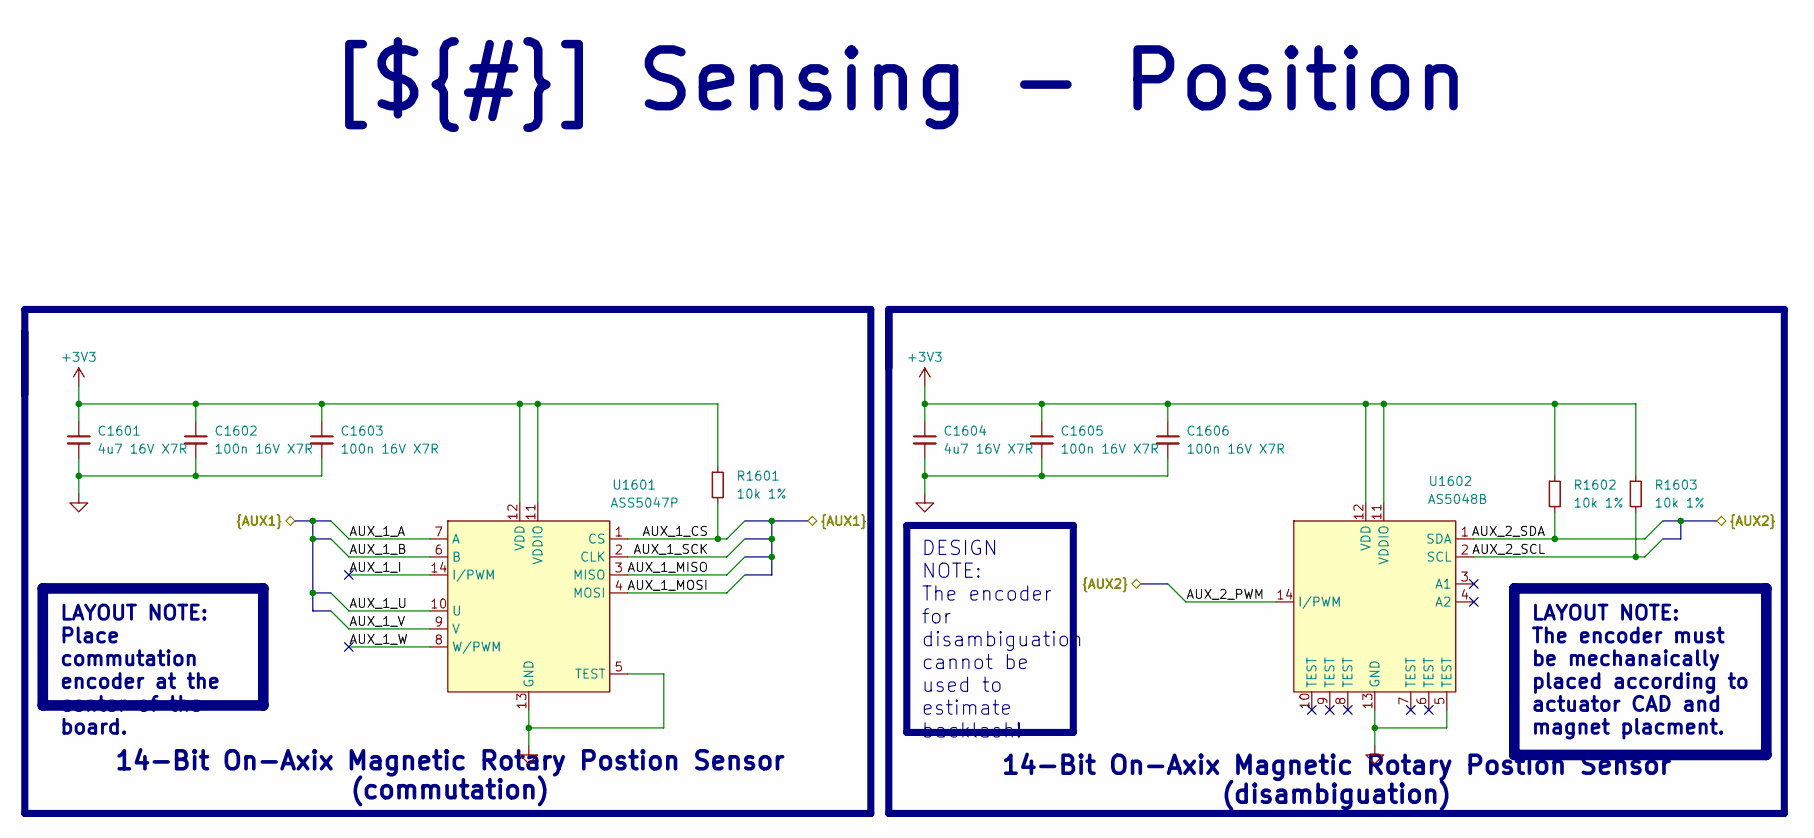
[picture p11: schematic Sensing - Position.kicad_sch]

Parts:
C1601, C1604: 4u7 16V X7R; C_0603_1608Metric; Manufacturer Part Number GRM188Z71C475KE21D
C1602, C1603, C1605, C1606: 100n 16V X7R; C_0402_1005Metric; Manufacturer Part Number C1005X7R1C104K050BC
R1601, R1602, R1603: 10k 1%; R_0402_1005Metric; Manufacturer Part Number ERJ-PA2F1002X
U1601: ASS5047P; SOP65P640X120-14N; Manufacturer Part Number AS5047P-ATSM
U1602: AS5048B; SOP65P640X120-14N; Manufacturer Part Number AS5048B-HTSP

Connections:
+3V3: C1601.1, C1602.1, C1603.1, C1604.1, C1605.1, C1606.1, R1601.1, R1602.1, R1603.1, U1601.11 (VDDIO), U1601.12 (VDD), U1602.11 (VDDIO), U1602.12 (VDD); also elsewhere on the board
/Project Architecture/Interface - Interconnects/AUX_1_A: U1601.7 (A); also elsewhere on the board
/Project Architecture/Interface - Interconnects/AUX_1_B: U1601.6 (B); also elsewhere on the board
/Project Architecture/Interface - Interconnects/AUX_1_CS: R1601.2, U1601.1 (CS); also elsewhere on the board
/Project Architecture/Interface - Interconnects/AUX_1_I: U1601.14 (I/PWM); also elsewhere on the board
/Project Architecture/Interface - Interconnects/AUX_1_MISO: U1601.3 (MISO); also elsewhere on the board
/Project Architecture/Interface - Interconnects/AUX_1_MOSI: U1601.4 (MOSI); also elsewhere on the board
/Project Architecture/Interface - Interconnects/AUX_1_SCK: U1601.2 (CLK); also elsewhere on the board
/Project Architecture/Interface - Interconnects/AUX_1_U: U1601.10 (U); also elsewhere on the board
/Project Architecture/Interface - Interconnects/AUX_1_V: U1601.9 (V); also elsewhere on the board
/Project Architecture/Interface - Interconnects/AUX_1_W: U1601.8 (W/PWM); also elsewhere on the board
/Project Architecture/Interface - Interconnects/AUX_2_PWM: U1602.14 (I/PWM); also elsewhere on the board
/Project Architecture/Interface - Interconnects/AUX_2_SCL: R1603.2, U1602.2 (SCL); also elsewhere on the board
/Project Architecture/Interface - Interconnects/AUX_2_SDA: R1602.2, U1602.1 (SDA); also elsewhere on the board
GND: C1601.2, C1602.2, C1603.2, C1604.2, C1605.2, C1606.2, U1601.5 (TEST), U1601.13 (GND), U1602.5 (TEST), U1602.13 (GND); also elsewhere on the board

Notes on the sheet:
14-Bit On-Axix Magnetic Rotary Postion Sensor (commutation)
[${#}] Sensing - Position
14-Bit On-Axix Magnetic Rotary Postion Sensor (disambiguation)
DESIGN NOTE: The encoder for disambiguation cannot be used to estimate backlash!
LAYOUT NOTE: Place commutation encoder at the center of the board.
LAYOUT NOTE: The encoder must be mechanaically placed according to actuator CAD and magnet placment.

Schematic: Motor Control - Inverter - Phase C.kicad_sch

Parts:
C1301, C1302: 22n 100V X7R; C_0805_2012Metric; Manufacturer Part Number KAM21BR72A223KM
C1304: 100n 100V X7R; C_1206_3216Metric; Manufacturer Part Number 885382208006
C1305: 10u 100V X7R; C_1210_3225Metric; Manufacturer Part Number C3225X7R2A106K250AC
D1301, D1302, D1303: BAT41KFILM; D_SOD-523; Manufacturer Part Number BAT41KFILM
J1301: PHASE_C; Pad_Square_Vias_6.5x6.5mm
NT1301, NT1302, NT1303: DIFF_PAIR; NetTie-2_SMD_Pad0.5mm
Q1301, Q1302: TPW1R306PL,L1Q; SOP_ADVANCE; Manufacturer Part Number TPW1R306PL,L1Q
R1301, R1302: 7R5 1%; R_0603_1608Metric; Manufacturer Part Number ERJ-U03F7R50V
R1303: 0m5 1% 2W; R_2512_6332Metric; Manufacturer Part Number PA2512FKE7W0R005E
R1304, R1305: 22R 1%; R_0805_2012Metric; Manufacturer Part Number ERJ-6ENF22R0V

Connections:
+VBAT_SAFE: C1304.1, C1305.1, Q1301.1 (D), R1304.1; also elsewhere on the board
/Project Architecture/Motor Control - Inverter - Phase A/DRIVER_GHC: D1301.1 (K), R1301.1; also elsewhere on the board
/Project Architecture/Motor Control - Inverter - Phase A/DRIVER_GLC: D1302.1 (K), R1302.1; also elsewhere on the board
/Project Architecture/Motor Control - Inverter - Phase A/DRIVER_SHC: NT1301.2; also elsewhere on the board
/Project Architecture/Motor Control - Inverter - Phase A/DRIVER_SPC+: NT1302.2; also elsewhere on the board
/Project Architecture/Motor Control - Inverter - Phase A/DRIVER_SPC-: NT1303.2; also elsewhere on the board
/Project Architecture/Motor Control - Inverter - Phase C/FET_GHC: D1301.2 (A), Q1301.2 (G), R1301.2
/Project Architecture/Motor Control - Inverter - Phase C/FET_GLC: D1302.2 (A), D1303.1 (K), Q1302.2 (G), R1302.2
/Project Architecture/Motor Control - Inverter - Phase C/PHASE_C: C1301.2, J1301.1, NT1301.1, Q1301.3 (S), Q1302.1 (D), R1305.1
/Project Architecture/Motor Control - Inverter - Phase C/PHASE_C_S: C1302.2, C1304.2, NT1302.1, Q1302.3 (S), R1303.1
GND: C1305.2, D1303.2 (A), NT1303.1, R1303.2; also elsewhere on the board
unnamed: C1301.1, R1304.2
unnamed: C1302.1, R1305.2

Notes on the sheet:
Flexible I/O worked examples
References:
Flexible I/O source configuration
Inverter Phase C
DESIGN NOTE: Low-Side Schottky diodes protect FET's gate against negavtive transients.
DESIGN NOTE: Local bulk and negative bounce tone sppression capacitors.
DESIGN NOTE: Optional RC snubber to reduce ringing.
[13] Motor Control - Inverter - Phase C
DESIGN NOTE: Gate resistor + dischrage diode.

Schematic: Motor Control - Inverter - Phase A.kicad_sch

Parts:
C1101, C1102: 22n 100V X7R; C_0805_2012Metric; Manufacturer Part Number KAM21BR72A223KM
C1103: 100n 100V X7R; C_1206_3216Metric; Manufacturer Part Number 885382208006
C1104: 10u 100V X7R; C_1210_3225Metric; Manufacturer Part Number C3225X7R2A106K250AC
D1101, D1102, D1103: BAT41KFILM; D_SOD-523; Manufacturer Part Number BAT41KFILM
J1101: PHASE_A; Pad_Square_Vias_6.5x6.5mm
NT1101, NT1102, NT1103: DIFF_PAIR; NetTie-2_SMD_Pad0.5mm
Q1101, Q1102: TPW1R306PL,L1Q; SOP_ADVANCE; Manufacturer Part Number TPW1R306PL,L1Q
R1101, R1102: 7R5 1%; R_0603_1608Metric; Manufacturer Part Number ERJ-U03F7R50V
R1103: 0m5 1% 2W; R_2512_6332Metric; Manufacturer Part Number PA2512FKE7W0R005E
R1104, R1105: 22R 1%; R_0805_2012Metric; Manufacturer Part Number ERJ-6ENF22R0V

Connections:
+VBAT_SAFE: C1103.1, C1104.1, Q1101.1 (D), R1104.1; also elsewhere on the board
/Project Architecture/Motor Control - Inverter - Phase A/DRIVER_GHA: D1101.1 (K), R1101.1; also elsewhere on the board
/Project Architecture/Motor Control - Inverter - Phase A/DRIVER_GLA: D1102.1 (K), R1102.1; also elsewhere on the board
/Project Architecture/Motor Control - Inverter - Phase A/DRIVER_SHA: NT1101.2; also elsewhere on the board
/Project Architecture/Motor Control - Inverter - Phase A/DRIVER_SPA+: NT1102.2; also elsewhere on the board
/Project Architecture/Motor Control - Inverter - Phase A/DRIVER_SPA-: NT1103.2; also elsewhere on the board
/Project Architecture/Motor Control - Inverter - Phase A/FET_GHA: D1101.2 (A), Q1101.2 (G), R1101.2
/Project Architecture/Motor Control - Inverter - Phase A/FET_GLA: D1102.2 (A), D1103.1 (K), Q1102.2 (G), R1102.2
/Project Architecture/Motor Control - Inverter - Phase A/PHASE_A: C1101.2, J1101.1, NT1101.1, Q1101.3 (S), Q1102.1 (D), R1105.1
/Project Architecture/Motor Control - Inverter - Phase A/PHASE_A_S: C1102.2, C1103.2, NT1102.1, Q1102.3 (S), R1103.1
GND: C1104.2, D1103.2 (A), NT1103.1, R1103.2; also elsewhere on the board
unnamed: C1101.1, R1104.2
unnamed: C1102.1, R1105.2

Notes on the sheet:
Flexible I/O worked examples
References:
Flexible I/O source configuration
DESIGN NOTE: Gate resistor + dischrage diode.
DESIGN NOTE: Low-Side Schottky diodes protect FET's gate against negavtive transients.
[${#}] Motor Control - Inverter - Phase A
DESIGN NOTE: Local bulk and negative bounce tone sppression capacitors.
DESIGN NOTE: Optional RC snubber to reduce ringing.
Inverter Phase A

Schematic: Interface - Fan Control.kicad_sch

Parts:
C1901: 4u7 16V X7R; C_0603_1608Metric; Manufacturer Part Number GRM188Z71C475KE21D
C1902: 100n 16V X7R; C_0402_1005Metric; Manufacturer Part Number C1005X7R1C104K050BC
Q1901: PMV90ENER; SOT-23; Manufacturer Part Number PMV90ENER
R1901: 10R 1%; R_0402_1005Metric; Manufacturer Part Number ERJ-PA2D10R0X
R1902: 10k 1%; R_0402_1005Metric; Manufacturer Part Number ERJ-PA2F1002X
U1901: DGD0216; SOT-23-5; Manufacturer Part Number DGD0216WT-7

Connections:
+3V3: C1901.1, C1902.1, U1901.5 (VCC); also elsewhere on the board
/Project Architecture/Interface - Fan Control/FAN_CONTROL_GATE: Q1901.2 (G), R1901.2, R1902.2
/Project Architecture/Interface - Fan Control/FAN_CONTROL_GATE_R: R1901.1, U1901.4 (OUT)
/Project Architecture/Interface - Fan Control/FAN_CONTROL_IN: U1901.3 (IN); also elsewhere on the board
/Project Architecture/Interface - Fan Control/FAN_CONTROL_PWM: Q1901.1 (D); also elsewhere on the board
GND: C1901.2, C1902.2, Q1901.3 (S), R1902.1, U1901.2 (COM); also elsewhere on the board

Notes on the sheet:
[${#}] Interface - Fan Control
Fan Gate Driver
DESIGN NOTE: Gate resistor should be chosen to slew rate of FET.
DESIGN NOTE: Gate driver is not strictly necsassary fpr hysteresos control, but could be useful for PWM control.

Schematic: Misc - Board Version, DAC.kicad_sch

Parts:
C2201: 100n 100V X7R; C_0603_1608Metric; Manufacturer Part Number KAF15BR72A104KT
R2201: DNP; R_0603_1608Metric; Manufacturer Part Number ERJ-UP3F1003V
R2202: 100k 1%; R_0603_1608Metric

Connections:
+3V3: R2201.2; also elsewhere on the board
/Project Architecture/MCU - I_O/BOARD_VERSION: C2201.1, R2201.1, R2202.2; also elsewhere on the board
GND: C2201.2, R2202.1; also elsewhere on the board

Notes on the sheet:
[${#}] ${TITLE}
Board Version Resistor Divider
DESIGN NOTE: V1 - TOP Resistor 100k BOTTOM DNP. V2 - BOTTOM Resistor 100k TOP DNP.

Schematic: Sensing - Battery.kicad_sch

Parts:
C1501: 100n 100V X7R; C_0603_1608Metric; Manufacturer Part Number KAF15BR72A104KT
R1501: 100k 1%; R_0603_1608Metric; Manufacturer Part Number ERJ-UP3F1003V
R1502: 4k7 1%; R_0603_1608Metric; Manufacturer Part Number ERJ-UP3F4701V

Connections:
+VBAT_SAFE: R1501.2; also elsewhere on the board
/Project Architecture/MCU - I_O/BATTERY_VSENSE: C1501.1, R1501.1, R1502.2; also elsewhere on the board
GND: C1501.2, R1502.1; also elsewhere on the board

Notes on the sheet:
[${#}] Sensing - Battery
DESIGN NOTE: 1/23 temperature stable voltage divider. Use low ppm resistors. 12S: max voltage: 2.19V. 8S: max voltage: 1.95V. 6S: max voltage: 1.46V.
Battery Sensing Voltage Divider

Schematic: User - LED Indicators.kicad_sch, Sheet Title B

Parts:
D2101, D2103: GREEN; LED_0402_1005Metric; Manufacturer Part Number FHD1105P-TR
D2102: RED; LED_0402_1005Metric; Manufacturer Part Number FHR1105P-TR
D2104: YELLOW; LED_0402_1005Metric; Manufacturer Part Number FHY1105P-TR
D2105: BLUE; LED_0402_1005Metric; Manufacturer Part Number 150040BS73220
D2106: ORAGNGE; LED_0402_1005Metric; Manufacturer Part Number SM0402OC
Q2101, Q2102: PMV90ENER; SOT-23; Manufacturer Part Number PMV90ENER
R2101, R2102, R2103, R2104, R2105, R2106, R2107, R2108, R2109, R2110: 10k 1%; R_0402_1005Metric; Manufacturer Part Number ERJ-PA2F1002X

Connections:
+3V3: R2107.2; also elsewhere on the board
+3V3A: R2108.2; also elsewhere on the board
+5V: R2103.2, R2106.2, R2109.2; also elsewhere on the board
+12V: R2110.2; also elsewhere on the board
/Project Architecture/MCU - I_O/LED_DBG_1: R2101.2; also elsewhere on the board
/Project Architecture/MCU - I_O/LED_DBG_2: R2104.2; also elsewhere on the board
/Project Architecture/User - LED Indicators/LED_1_GATE: Q2101.2 (G), R2101.1, R2102.2
/Project Architecture/User - LED Indicators/LED_2_GATE: Q2102.2 (G), R2104.1, R2105.2
/Project Architecture/User - LED Indicators/LED_DBG_1_A: D2101.2 (A), R2103.1
/Project Architecture/User - LED Indicators/LED_DBG_1_K: D2101.1 (K), Q2101.1 (D)
/Project Architecture/User - LED Indicators/LED_DBG_2_A: D2102.2 (A), R2106.1
/Project Architecture/User - LED Indicators/LED_DBG_2_K: D2102.1 (K), Q2102.1 (D)
/Project Architecture/User - LED Indicators/PWR_ON_3V3: D2103.2 (A), R2107.1
/Project Architecture/User - LED Indicators/PWR_ON_3V3A: D2104.2 (A), R2108.1
/Project Architecture/User - LED Indicators/PWR_ON_5V: D2105.2 (A), R2109.1
/Project Architecture/User - LED Indicators/PWR_ON_12V: D2106.2 (A), R2110.1
GND: D2103.1 (K), D2104.1 (K), D2105.1 (K), D2106.1 (K), Q2101.3 (S), Q2102.3 (S), R2102.1, R2105.1; also elsewhere on the board

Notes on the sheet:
Debug LED's
Power On Led's
[${#}] User - LED Indicators

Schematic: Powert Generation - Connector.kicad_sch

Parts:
D401: SMBJ51CA-E3/52; D_SMB; Manufacturer Part Number SMBJ51CA-E3/52
J401: XT60; AMASS_XT60PW-F_1x02_P7.20mm_Horizontal

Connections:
+VBAT_SAFE: D401.1 (K), J401.1; also elsewhere on the board
GND: D401.2 (A), J401.2; also elsewhere on the board

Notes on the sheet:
DESIGN NOTE: Do not hot-plug when powered!
Power Supply Input Protection
LAYOUT NOTE: Place ESD diode near input power connectors.
[${#}] Powert Generation - Connector
LAYOUT NOTE: Keep sufficent clearence between power nets according to ICP-2221.
DESIGN NOTE: Do not exceed absolute maximum rating! Maximum input voltage is 44V (10S).

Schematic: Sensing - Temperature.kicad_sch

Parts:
C1401, C1402: 100n 100V X7R; C_0603_1608Metric; Manufacturer Part Number KAF15BR72A104KT
D1401, D1402: BAT41KFILM; D_SOD-523; Manufacturer Part Number BAT41KFILM
NT1401: NTC_MOT_H; NetTie-2_SMD_Pad0.5mm
NT1402: NTC_MOT_L; NetTie-2_SMD_Pad0.5mm
R1402, R1403: 10k 1%; R_0603_1608Metric; Manufacturer Part Number ERJ-PA3F1002V
TH1401: 47k 1% NTC; R_0603_1608Metric; Manufacturer Part Number NCU18WB473D6SRB

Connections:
+3V3A: D1401.1 (K), D1402.1 (K); also elsewhere on the board
+VBAT_SAFE: NT1401.2, TH1401.1; also elsewhere on the board
/Project Architecture/Interface - Interconnects/TEMP_MOT_H: NT1401.1; also elsewhere on the board
/Project Architecture/Interface - Interconnects/TEMP_MOT_L: NT1402.1; also elsewhere on the board
/Project Architecture/MCU - I_O/SENSE_TEMP_FET: C1401.1, D1401.2 (A), R1402.2, TH1401.2; also elsewhere on the board
/Project Architecture/MCU - I_O/SENSE_TEMP_MOT: C1402.1, D1402.2 (A), NT1402.2, R1403.2; also elsewhere on the board
GND: C1401.2, C1402.2, R1402.1, R1403.1; also elsewhere on the board

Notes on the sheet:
DESIGN NOTE: Nominal B-Constant 4050-4090K.
[${#}] Sensing - Temperature
DESIGN NOTE: Optionally it is possible to add an external thermistor. Not critical for proper operation.
Mosfet and Motor Temperature Sensing
LAYOUT NOTE: NTC's must be placed close and thermally coupled to relevant heat source. Route away from noisy traces.

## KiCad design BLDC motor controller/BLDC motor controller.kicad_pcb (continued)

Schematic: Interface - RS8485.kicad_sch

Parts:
C1701: 4u7 16V X7R; C_0603_1608Metric; Manufacturer Part Number GRM188Z71C475KE21D
C1702: 100n 16V X7R; C_0402_1005Metric; Manufacturer Part Number C1005X7R1C104K050BC
R1701, R1702: 10k 1%; R_0402_1005Metric; Manufacturer Part Number ERJ-PA2F1002X
R1703, R1705: 390R 1%; R_0402_1005Metric; Manufacturer Part Number ERJ-PA2D3900X
R1704: 120R; R_0402_1005Metric; Manufacturer Part Number ERJ-PA2D1200X
U1701: SP3494; SOIC-8_3.9x4.9mm_P1.27mm; Manufacturer Part Number SP3494EN-L

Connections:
+3V3: C1701.1, C1702.1, R1701.1, R1703.1, U1701.8 (VSS); also elsewhere on the board
/Project Architecture/Interface - Interconnects/RS485_N: R1704.2, R1705.1, U1701.7 (B); also elsewhere on the board
/Project Architecture/Interface - Interconnects/RS485_P: R1703.2, R1704.1, U1701.6 (A); also elsewhere on the board
/Project Architecture/Interface - RS8485/RS485_UART_DE: R1701.2, U1701.3 (DE); also elsewhere on the board
/Project Architecture/Interface - RS8485/RS485_UART_N: U1701.1 (RO); also elsewhere on the board
/Project Architecture/Interface - RS8485/RS485_UART_P: U1701.4 (DI); also elsewhere on the board
/Project Architecture/Interface - RS8485/RS485_UART_nRE: R1702.1, U1701.2 (nRE); also elsewhere on the board
GND: C1701.2, C1702.2, R1702.2, R1705.2, U1701.5 (GND); also elsewhere on the board

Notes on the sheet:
[${#}] Interface - RS8485
LAYOUT NOTE: Place close to RS485 connector.
UART - RS485 Half Duplex Inteface

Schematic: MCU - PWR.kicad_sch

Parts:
C801: 1u 16V X7R; C_0603_1608Metric; Manufacturer Part Number EMK107B7105KA8T
C802, C807, C808, C810: 4u7 16V X7R; C_0603_1608Metric; Manufacturer Part Number GRM188Z71C475KE21D
C803, C804, C805, C806, C809, C811: 100n 16V X7R; C_0402_1005Metric; Manufacturer Part Number C1005X7R1C104K050BC
FB801: 1k @100MHz; L_0805_2012Metric; Manufacturer Part Number ACML-0805H-102-T
U801_901: STM32G474RET6; QFP50P1200X1200X160-64N; Manufacturer Part Number STM32G474RET6

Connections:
+3V3: C801.1, C802.1, C803.1, C804.1, C805.1, C806.1, U801_901.1 (VBAT), U801_901.15 (VDD), U801_901.32 (VDD), U801_901.48 (VDD), U801_901.64 (VDD); also elsewhere on the board
+3V3A: C807.1, FB801.1; also elsewhere on the board
+3V3A_FILT: C808.1, C809.1, C810.1, C811.1, FB801.2, U801_901.28 (VREF+), U801_901.29 (VDDA)
GND: C801.2, C802.2, C803.2, C804.2, C805.2, C806.2, C807.2, C808.2, C809.2, C810.2, C811.2, U801_901.16 (VSS), U801_901.27 (VSSA), U801_901.31 (VSS), U801_901.47 (VSS), U801_901.63 (VSS); also elsewhere on the board

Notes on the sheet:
LAYOUT NOTE: Place all cpaacitors to relevant pin. Minimize loop inductance.
[${#}] MCU - PWR
Microcontroller Power Supply Scheme

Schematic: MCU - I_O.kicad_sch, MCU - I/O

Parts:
R901: 10k 1%; R_0603_1608Metric; Manufacturer Part Number ERJ-PA3F1002V
TP901, TP902, TP903, TP904, TP905, TP906, TP907, TP908, TP909, TP910, TP911, TP912, TP913: AUX; TestPoint_Pad_1.0x1.0mm
TP914, TP915, TP916, TP917, TP918, TP919, TP920, TP921, TP922, TP923, TP924, TP925, TP926: DRIVER; TestPoint_Pad_D1.0mm
TP927, TP928: TEMP; TestPoint_Pad_1.0x1.0mm
TP929: BATEERY; TestPoint_Pad_1.0x1.0mm
TP930, TP931, TP932, TP933: FD_CAN; TestPoint_Pad_1.0x1.0mm
TP934, TP935, TP936, TP937: RS485; TestPoint_Pad_1.0x1.0mm
TP938: FAN; TestPoint_Pad_1.0x1.0mm
TP939, TP940, TP941: HAL; TestPoint_Pad_D1.0mm
U801_901: STM32G474RET6; QFP50P1200X1200X160-64N; Manufacturer Part Number STM32G474RET6

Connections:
/Project Architecture/Interface - FD-CAN/CAN_MCU_N: TP931.1, U801_901.45 (PA11); also elsewhere on the board
/Project Architecture/Interface - FD-CAN/CAN_MCU_P: TP930.1, U801_901.46 (PA12); also elsewhere on the board
/Project Architecture/Interface - FD-CAN/CAN_S: TP933.1, U801_901.41 (PC9); also elsewhere on the board
/Project Architecture/Interface - FD-CAN/CAN_SHDN: TP932.1, U801_901.40 (PC8); also elsewhere on the board
/Project Architecture/Interface - Fan Control/FAN_CONTROL_IN: TP938.1, U801_901.11 (PC3); also elsewhere on the board
/Project Architecture/Interface - Interconnects/AUX_1_A: TP906.1, U801_901.57 (PB4); also elsewhere on the board
/Project Architecture/Interface - Interconnects/AUX_1_B: TP905.1, U801_901.58 (PB5); also elsewhere on the board
/Project Architecture/Interface - Interconnects/AUX_1_CS: TP910.1, U801_901.51 (PA15); also elsewhere on the board
/Project Architecture/Interface - Interconnects/AUX_1_I: TP904.1; also elsewhere on the board
/Project Architecture/Interface - Interconnects/AUX_1_MISO: TP908.1, U801_901.52 (PC10); also elsewhere on the board
/Project Architecture/Interface - Interconnects/AUX_1_MOSI: TP909.1, U801_901.53 (PC11); also elsewhere on the board
/Project Architecture/Interface - Interconnects/AUX_1_SCK: TP907.1, U801_901.54 (PC12); also elsewhere on the board
/Project Architecture/Interface - Interconnects/AUX_1_U: TP903.1, U801_901.59 (PB6); also elsewhere on the board
/Project Architecture/Interface - Interconnects/AUX_1_V: TP902.1, U801_901.55 (PD2); also elsewhere on the board
/Project Architecture/Interface - Interconnects/AUX_1_W: TP901.1; also elsewhere on the board
/Project Architecture/Interface - Interconnects/AUX_2_PWM: TP911.1, U801_901.62 (PB9); also elsewhere on the board
/Project Architecture/Interface - Interconnects/AUX_2_SCL: TP912.1, U801_901.43 (PA9); also elsewhere on the board
/Project Architecture/Interface - Interconnects/AUX_2_SDA: TP913.1, U801_901.42 (PA8); also elsewhere on the board
/Project Architecture/Interface - Interconnects/MCU_SWCLK: U801_901.50 (PA14); also elsewhere on the board
/Project Architecture/Interface - Interconnects/MCU_SWDIO: U801_901.49 (PA13); also elsewhere on the board
/Project Architecture/Interface - Interconnects/MCU_SWO: U801_901.56 (PB3); also elsewhere on the board
/Project Architecture/Interface - Interconnects/MCU_nRESET: U801_901.7 (PG10); also elsewhere on the board
/Project Architecture/Interface - Interconnects/POSITON_A: TP939.1, U801_901.39 (PC7); also elsewhere on the board
/Project Architecture/Interface - Interconnects/POSITON_B: TP940.1, U801_901.38 (PC6); also elsewhere on the board
/Project Architecture/Interface - Interconnects/POSITON_C: TP941.1, U801_901.37 (PB15); also elsewhere on the board
/Project Architecture/Interface - RS8485/RS485_UART_DE: TP934.1, U801_901.13 (PA1); also elsewhere on the board
/Project Architecture/Interface - RS8485/RS485_UART_N: TP936.1, U801_901.17 (PA3); also elsewhere on the board
/Project Architecture/Interface - RS8485/RS485_UART_P: TP937.1, U801_901.14 (PA2); also elsewhere on the board
/Project Architecture/Interface - RS8485/RS485_UART_nRE: TP935.1, U801_901.12 (PA0); also elsewhere on the board
/Project Architecture/MCU - I_O/BATTERY_VSENSE: TP929.1, U801_901.9 (PC1); also elsewhere on the board
/Project Architecture/MCU - I_O/BOARD_VERSION: U801_901.5 (PF0); also elsewhere on the board
/Project Architecture/MCU - I_O/DRIVER_CS: TP921.1, U801_901.18 (PA4); also elsewhere on the board
/Project Architecture/MCU - I_O/DRIVER_ENABLE: TP926.1, U801_901.22 (PC4); also elsewhere on the board
/Project Architecture/MCU - I_O/DRIVER_HIZ: TP917.1, U801_901.23 (PC5); also elsewhere on the board
/Project Architecture/MCU - I_O/DRIVER_MISO: TP919.1, U801_901.20 (PA6); also elsewhere on the board
/Project Architecture/MCU - I_O/DRIVER_MOSI: TP918.1, U801_901.21 (PA7); also elsewhere on the board
/Project Architecture/MCU - I_O/DRIVER_NFALUT: TP925.1, U801_901.30 (PB10); also elsewhere on the board
/Project Architecture/MCU - I_O/DRIVER_SCK: TP920.1, U801_901.19 (PA5); also elsewhere on the board
/Project Architecture/MCU - I_O/FILTERED_SOA: TP922.1, U801_901.33 (PB11); also elsewhere on the board
/Project Architecture/MCU - I_O/FILTERED_SOB: TP923.1, U801_901.34 (PB12); also elsewhere on the board
/Project Architecture/MCU - I_O/FILTERED_SOC: TP924.1, U801_901.35 (PB13); also elsewhere on the board
/Project Architecture/MCU - I_O/LED_DBG_1: U801_901.3 (PC14); also elsewhere on the board
/Project Architecture/MCU - I_O/LED_DBG_2: U801_901.4 (PC15); also elsewhere on the board
/Project Architecture/MCU - I_O/MCU_BOOT: R901.2, U801_901.61 (PB8)
/Project Architecture/MCU - I_O/PWM_PHASE_A: TP916.1, U801_901.24 (PB0); also elsewhere on the board
/Project Architecture/MCU - I_O/PWM_PHASE_B: TP915.1, U801_901.25 (PB1); also elsewhere on the board
/Project Architecture/MCU - I_O/PWM_PHASE_C: TP914.1, U801_901.26 (PB2); also elsewhere on the board
/Project Architecture/MCU - I_O/SENSE_TEMP_FET: TP928.1, U801_901.10 (PC2); also elsewhere on the board
/Project Architecture/MCU - I_O/SENSE_TEMP_MOT: TP927.1, U801_901.8 (PC0); also elsewhere on the board
GND: R901.1; also elsewhere on the board

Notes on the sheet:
Shunt outputs filtered
Half bridge PWMs
Do not forget flash optlon bytes when flashing for the first time.
Temperature Sense Connection
Auxiliary port 1
BOOT Pin Configuration
[${#}] MCU - I/O
Fan Control Connection
RS485 Connection
Battery Sense Connection
Debug Led's
Connection to Gate Driver
SWD Debug/Programming
SPI for DRV config
Auxiliary port 2
External Enocder
Motor enable and fault
FD-CAN Connection
Test Points
Microcontroller I/O Pins
Auxiliary Ports
Board Version

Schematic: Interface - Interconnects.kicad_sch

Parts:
C2001, C2003, C2009, C2011, C2015, C2024: 4u7 16V X7R; C_0603_1608Metric; Manufacturer Part Number GRM188Z71C475KE21D
C2002, C2004, C2010, C2012, C2016, C2022: 100n 16V X7R; C_0402_1005Metric; Manufacturer Part Number C1005X7R1C104K050BC
C2005, C2006, C2007, C2008, C2013, C2014, C2021, C2023, C2025: DNP; C_0603_1608Metric; not fitted
C2017: 2u2 100V X7R; C_0805_2012Metric; Manufacturer Part Number CGA4J1X7R2A225K125AC
C2018: 100n 100V X7R; C_0603_1608Metric; Manufacturer Part Number KAF15BR72A104KT
D1403, D1404, D1405: BAT41KFILM; D_SOD-523; Manufacturer Part Number BAT41KFILM
D2001, D2004: ESDR0524SMUTAG; Manufacturer Part Number ESDR0524SMUTAG
D2002, D2003, D2005, D2006: DF3A5.6LFU,LF; SOT-23-3; Manufacturer Part Number DF3A5.6LFU,LF
D2007: CG0402MLC-3.3LG; D_0402_1005Metric; Manufacturer Part Number CG0402MLC-3.3LG
D2009, D2010, D2011: CG0402MLC-12G; D_0402_1005Metric; Manufacturer Part Number CG0402MLC-12LG
J2001: Conn_01x07; Molex_PicoBlade_53048-0710_1x07_P1.25mm_Horizontal; Manufacturer Part Number 53048-0710
J2004, J2005, J2008, J2009: Conn_01x03; Molex_PicoBlade_53048-0310_1x03_P1.25mm_Horizontal; Manufacturer Part Number 53048-0310
J2007: Conn_ARM_SWD_TagConnect_TC2030-NL; Tag-Connect_TC2030-IDC-NL_2x03_P1.27mm_Vertical
J2011, J2012: Conn_01x02; Molex_PicoBlade_53048-0210_1x02_P1.25mm_Horizontal; Manufacturer Part Number 53048-0210
J2202: Conn_01x05; Molex_PicoBlade_53048-0510_1x05_P1.25mm_Horizontal; Manufacturer Part Number 53048-0510
J2203: Conn_01x05; Molex_PicoBlade_53261-0571_1x05-1MP_P1.25mm_Horizontal; Manufacturer Part Number 53261-0571
R1903, R1904, R1905: 10k 1%; R_0603_1608Metric; Manufacturer Part Number ERJ-PA3F1002V
R2001, R2002, R2003, R2004, R2006, R2007, R2010, R2012, R2013: 100R 1%; R_0603_1608Metric; Manufacturer Part Number ERJ-UP3F1000V
R2008, R2009, R2011, R20010: 22R 1%; R_0402_1005Metric; Manufacturer Part Number ERJ-PA2F22R0X

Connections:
+3V3: C2003.1, C2004.1, C2011.1, C2012.1, C2015.1, C2016.1, D1403.1 (K), D1404.1 (K), D1405.1 (K), J2001.1, J2007.1 (VCC), J2202.1, R1903.2, R1904.2, R1905.2; also elsewhere on the board
+5V: C2001.1, C2002.1, C2009.1, C2010.1, C2022.1, C2024.1, J2001.2, J2202.2, J2203.1; also elsewhere on the board
+12V: C2017.1, C2018.1, J2012.2; also elsewhere on the board
/Project Architecture/Interface - FD-CAN/FDCAN_N: D2003.1 (K), J2004.3, J2005.1; also elsewhere on the board
/Project Architecture/Interface - FD-CAN/FDCAN_P: D2003.2 (K), J2004.1, J2005.3; also elsewhere on the board
/Project Architecture/Interface - Fan Control/FAN_CONTROL_PWM: D2007.1 (K), J2012.1; also elsewhere on the board
/Project Architecture/Interface - Interconnects/AUXP_1_CS: D2001.5 (K), J2001.3, R2001.2
/Project Architecture/Interface - Interconnects/AUXP_1_MISO: D2001.4, J2001.4, R2002.2
/Project Architecture/Interface - Interconnects/AUXP_1_MOSI: D2001.2, J2001.5, R2003.2
/Project Architecture/Interface - Interconnects/AUXP_1_SCK: D2001.1 (K), J2001.6, R2004.2
/Project Architecture/Interface - Interconnects/AUXP_2_SCL: D2002.2 (K), J2202.4, R2007.2
/Project Architecture/Interface - Interconnects/AUXP_2_SDA: D2002.1 (K), J2202.3, R2006.2
/Project Architecture/Interface - Interconnects/AUX_1_CS: C2005.1, R2001.1; also elsewhere on the board
/Project Architecture/Interface - Interconnects/AUX_1_MISO: C2006.1, R2002.1; also elsewhere on the board
/Project Architecture/Interface - Interconnects/AUX_1_MOSI: C2007.1, R2003.1; also elsewhere on the board
/Project Architecture/Interface - Interconnects/AUX_1_SCK: C2008.1, R2004.1; also elsewhere on the board
/Project Architecture/Interface - Interconnects/AUX_2_SCL: C2013.1, R2007.1; also elsewhere on the board
/Project Architecture/Interface - Interconnects/AUX_2_SDA: C2014.1, R2006.1; also elsewhere on the board
/Project Architecture/Interface - Interconnects/MCU_SWCLK: R2009.1; also elsewhere on the board
/Project Architecture/Interface - Interconnects/MCU_SWDIO: R20010.1; also elsewhere on the board
/Project Architecture/Interface - Interconnects/MCU_SWO: R2011.1; also elsewhere on the board
/Project Architecture/Interface - Interconnects/MCU_nRESET: R2008.1; also elsewhere on the board
/Project Architecture/Interface - Interconnects/POSITON_A: C2025.1, D1405.2 (A), R1903.1, R2010.1; also elsewhere on the board
/Project Architecture/Interface - Interconnects/POSITON_A_P: D2010.1 (K), J2203.2, R2010.2
/Project Architecture/Interface - Interconnects/POSITON_B: C2023.1, D1404.2 (A), R1904.1, R2012.1; also elsewhere on the board
/Project Architecture/Interface - Interconnects/POSITON_B_P: D2009.1 (K), J2203.3, R2012.2
/Project Architecture/Interface - Interconnects/POSITON_C: C2021.1, D1403.2 (A), R1905.1, R2013.1; also elsewhere on the board
/Project Architecture/Interface - Interconnects/POSITON_C_P: D2011.1 (K), J2203.4, R2013.2
/Project Architecture/Interface - Interconnects/RS485_N: D2005.1 (K), J2008.3, J2009.1; also elsewhere on the board
/Project Architecture/Interface - Interconnects/RS485_P: D2005.2 (K), J2008.1, J2009.3; also elsewhere on the board
/Project Architecture/Interface - Interconnects/SWCLK: D2004.2, J2007.4 (SWCLK), R2009.2
/Project Architecture/Interface - Interconnects/SWDIO: D2004.4, J2007.2 (SWDIO), R20010.2
/Project Architecture/Interface - Interconnects/SWO: D2004.1 (K), J2007.6 (SWO), R2011.2
/Project Architecture/Interface - Interconnects/TEMP_MOT_H: D2006.2 (K), J2011.2; also elsewhere on the board
/Project Architecture/Interface - Interconnects/TEMP_MOT_L: D2006.1 (K), J2011.1; also elsewhere on the board
/Project Architecture/Interface - Interconnects/nRESET: D2004.5 (K), J2007.3 (~RESET), R2008.2
GND: C2001.2, C2002.2, C2003.2, C2004.2, C2005.2, C2006.2, C2007.2, C2008.2, C2009.2, C2010.2, C2011.2, C2012.2, C2013.2, C2014.2, C2015.2, C2016.2, C2017.2, C2018.2, C2021.2, C2022.2, C2023.2, C2024.2, C2025.2, D2001.3, D2002.3 (A), D2003.3 (A), D2004.3, D2005.3 (A), D2006.3 (A), D2007.2 (A), D2009.2 (A), D2010.2 (A), D2011.2 (A), J2001.7, J2004.2, J2005.2, J2007.5 (GND), J2008.2, J2009.2, J2202.5, J2203.5; also elsewhere on the board

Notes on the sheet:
LAYOUT NOTE: Place filter near to connector
DESIGN NOTE: Optinally popiulate capacitors if excessive noise seen on the pins.
DESIGN NOTE: Only connect GND if connected device does not share ground!
12V Fan Connector
[${#}] Interface - Interconnects
DESIGN NOTE: Do not exceed maximum ratings for pin voltages!
Motor Temperature Sensing Thermistor Connector
SWD Debug/Programming Inzerface
Auxilliary Connector AUX1
Auxilliary Connector AUX2
LAYOUT NOTE: FDCAN should be routed as a 120-ohm differential pair.
FD CAN Connector
RS485 Connector
LAYOUT NOTE: FDCAN should be routed as a 100-ohm differential pair.
DESIGN NOTE: Ideally connect thermistor with nominal B-Constant 4050-4099K.
HAL Sensor Connector

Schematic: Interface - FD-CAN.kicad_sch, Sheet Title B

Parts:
C1703, C1801: 4u7 16V X7R; C_0603_1608Metric; Manufacturer Part Number GRM188Z71C475KE21D
C1802: 100n 16V X7R; C_0402_1005Metric; Manufacturer Part Number C1005X7R1C104K050BC
R1801, R1802: 10k 1%; R_0402_1005Metric; Manufacturer Part Number ERJ-PA2F1002X
R1803, R1804: 60R4 1% 1/4W; R_0603_1608Metric; Manufacturer Part Number ERJ-UP3F60R4V
SW2001: CAS-220TA; SW_DPDT_CK_JS202011JCQN; Manufacturer Part Number CAS-220TA
U1801: TCAN330; SOIC-8_3.9x4.9mm_P1.27mm; Manufacturer Part Number TCAN330GDR

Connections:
+3V3: C1801.1, C1802.1, U1801.3 (VCC); also elsewhere on the board
/Project Architecture/Interface - FD-CAN/CAN_MCU_N: U1801.4 (RXD); also elsewhere on the board
/Project Architecture/Interface - FD-CAN/CAN_MCU_P: U1801.1 (TXD); also elsewhere on the board
/Project Architecture/Interface - FD-CAN/CAN_S: R1801.1, U1801.8 (S); also elsewhere on the board
/Project Architecture/Interface - FD-CAN/CAN_SHDN: R1802.1, U1801.5 (SHDN); also elsewhere on the board
/Project Architecture/Interface - FD-CAN/FDCAN_N: R1804.2, SW2001.3 (C); also elsewhere on the board
/Project Architecture/Interface - FD-CAN/FDCAN_P: R1803.1, SW2001.6 (C); also elsewhere on the board
/Project Architecture/Interface - FD-CAN/FDCAN_TERM_MID: C1703.1, R1803.2, R1804.1
/Project Architecture/Interface - FD-CAN/FDCAN_TN: SW2001.2 (B), U1801.6 (CANL)
/Project Architecture/Interface - FD-CAN/FDCAN_TP: SW2001.5 (B), U1801.7 (CANH)
GND: C1703.2, C1801.2, C1802.2, R1801.2, R1802.2, U1801.2 (GND); also elsewhere on the board

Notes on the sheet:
Flexible I/O worked examples
References:
Flexible I/O source configuration
High Speed FD-CAN Transiver
[${#}] Interface - FD-CAN
LAYOUT NOTE: Place close to FDCAN connector.
DESIGN NOTE: Silent mode and Shutdown are disabled.

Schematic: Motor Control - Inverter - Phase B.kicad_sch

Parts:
C1201, C1202: 22n 100V X7R; C_0805_2012Metric; Manufacturer Part Number KAM21BR72A223KM
C1203: 100n 100V X7R; C_1206_3216Metric; Manufacturer Part Number 885382208006
C1204: 10u 100V X7R; C_1210_3225Metric; Manufacturer Part Number C3225X7R2A106K250AC
D1201, D1202, D1203: BAT41KFILM; D_SOD-523; Manufacturer Part Number BAT41KFILM
J1201: PHASE_B; Pad_Square_Vias_6.5x6.5mm
NT1201, NT1202, NT1203: DIFF_PAIR; NetTie-2_SMD_Pad0.5mm
Q1201, Q1202: TPW1R306PL,L1Q; SOP_ADVANCE; Manufacturer Part Number TPW1R306PL,L1Q
R1201, R1202: 7R5 1%; R_0603_1608Metric; Manufacturer Part Number ERJ-U03F7R50V
R1203: 0m5 1% 2W; R_2512_6332Metric; Manufacturer Part Number PA2512FKE7W0R005E
R1204, R1205: 22R 1%; R_0805_2012Metric; Manufacturer Part Number ERJ-6ENF22R0V

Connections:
+VBAT_SAFE: C1203.1, C1204.1, Q1201.1 (D), R1204.1; also elsewhere on the board
/Project Architecture/Motor Control - Inverter - Phase A/DRIVER_GHB: D1201.1 (K), R1201.1; also elsewhere on the board
/Project Architecture/Motor Control - Inverter - Phase A/DRIVER_GLB: D1202.1 (K), R1202.1; also elsewhere on the board
/Project Architecture/Motor Control - Inverter - Phase A/DRIVER_SHB: NT1201.2; also elsewhere on the board
/Project Architecture/Motor Control - Inverter - Phase A/DRIVER_SPB+: NT1202.2; also elsewhere on the board
/Project Architecture/Motor Control - Inverter - Phase A/DRIVER_SPB-: NT1203.2; also elsewhere on the board
/Project Architecture/Motor Control - Inverter - Phase B/FET_GHB: D1201.2 (A), Q1201.2 (G), R1201.2
/Project Architecture/Motor Control - Inverter - Phase B/FET_GLB: D1202.2 (A), D1203.1 (K), Q1202.2 (G), R1202.2
/Project Architecture/Motor Control - Inverter - Phase B/PHASE_B: C1201.2, J1201.1, NT1201.1, Q1201.3 (S), Q1202.1 (D), R1205.1
/Project Architecture/Motor Control - Inverter - Phase B/PHASE_B_S: C1202.2, C1203.2, NT1202.1, Q1202.3 (S), R1203.1
GND: C1204.2, D1203.2 (A), NT1203.1, R1203.2; also elsewhere on the board
unnamed: C1201.1, R1204.2
unnamed: C1202.1, R1205.2

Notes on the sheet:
Flexible I/O worked examples
References:
Flexible I/O source configuration
Inverter Phase B
DESIGN NOTE: Optional RC snubber to reduce ringing.
DESIGN NOTE: Local bulk and negative bounce tone sppression capacitors.
[12] Motor Control - Inverter - Phase B
DESIGN NOTE: Gate resistor + dischrage diode.
DESIGN NOTE: Low-Side Schottky diodes protect FET's gate against negavtive transients.

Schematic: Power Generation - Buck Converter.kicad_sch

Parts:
C601, C602, C603, C609, C610, C611, C617, C618: 2u2 100V X7R; C_1210_3225Metric; Manufacturer Part Number C1210C225J1RACAUTO
C604, C606, C612, C614, C620: 100n 100V X7R; C_0805_2012Metric; Manufacturer Part Number 08051C104JAZ2A
C605, C613: 1u 50V X7R; C_0805_2012Metric; Manufacturer Part Number 08055C105JAT2A
C607, C615: 22u 25V X7R; C_1210_3225Metric; Manufacturer Part Number MSAST32MSB7226KPNB25
C608, C616: 100n 25V X7R; C_0603_1608Metric; Manufacturer Part Number C0603C104J3RECAUTO7411
C619: 10u 25V X7R; C_1210_3225Metric; Manufacturer Part Number GRM32DR71E106KA12K
C622: 22u 16V X7R; C_1210_3225Metric; Manufacturer Part Number MSAST32MSB7226KPNB25
C623: 100n 25V X7R; C_0805_2012Metric; Manufacturer Part Number 08053C104KAZ2A
F603: 1k @100MHz; L_0805_2012Metric; Manufacturer Part Number ACML-0805H-102-T
FB601, FB602: 1k @100MHz; L_0805_2012Metric; Manufacturer Part Number ACML-0805H-102-T
L601, L602: 22u; L_Coilcraft_LPS4018; Manufacturer Part Number LPS4018-223MRC
L603: 2u2; L_Coilcraft_LPS3314; Manufacturer Part Number LPS3314-222MRC
NT601: FB_5V; NetTie-2_SMD_Pad0.5mm
NT602: EN_3V3; NetTie-2_SMD_Pad0.5mm
NT603: VOS_3V3; NetTie-2_SMD_Pad0.5mm
NT604: FB_3V3; NetTie-2_SMD_Pad0.5mm
R601, R605: 140k 1%; R_0603_1608Metric; Manufacturer Part Number ERJ-PA3F1403V
R602, R604, R606, R608, R611: 10k 1%; R_0603_1608Metric; Manufacturer Part Number ERJ-PA3F1002V
R603, R607: 0R; R_0603_1608Metric; Manufacturer Part Number ERJ-H3G0R00V
R609: 100k 1%; R_0603_1608Metric; Manufacturer Part Number ERJ-UP3F1003V
R610: 9k9 1%; R_0603_1608Metric; Manufacturer Part Number ERJ-UP3F9531V
TP601, TP602, TP603: +VBAT; TestPoint_Pad_1.0x1.0mm
TP604: VIN_3V3; TestPoint_Pad_1.0x1.0mm
TP605: VIN_5V; TestPoint_Pad_1.0x1.0mm
TP606: VIN_12V; TestPoint_Pad_1.0x1.0mm
TP607, TP608: +12V; TestPoint_Pad_1.0x1.0mm
TP609, TP610: +5V; TestPoint_Pad_1.0x1.0mm
TP611, TP612: +3V3; TestPoint_Pad_1.0x1.0mm
TP613, TP614, TP615: GND; TestPoint_Pad_1.0x1.0mm
U601: LMR36506MSC5RPERQ1; Manufacturer Part Number LMR36506MSC5RPERQ1
U602: LMR36506MSCQRPERQ1; LMR36506MSC5RPERQ1; Manufacturer Part Number LMR36506MSCQRPERQ1
U603: TPS62172; SON50P200X200X80-9N; Manufacturer Part Number TPS62172QDSGRQ1

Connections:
+3V3: C622.1, C623.1, L603.2, NT603.1, R611.1, TP611.1, TP612.1; also elsewhere on the board
+5V: C607.1, C608.1, C617.1, F603.1, L601.2, NT601.2, R604.1, TP609.1, TP610.1; also elsewhere on the board
+12V: C615.1, C616.1, L602.2, R608.1, R609.1, TP607.1, TP608.1; also elsewhere on the board
+VBAT_FILT_3V3_IN: C618.1, C619.1, C620.1, F603.2, NT602.1, TP604.1, U603.2 (VIN)
+VBAT_FILT_5V_IN: C602.1, C603.1, C604.1, FB601.2, R601.1, TP605.1, U601.4 (VIN)
+VBAT_FILT_12V_IN: C610.1, C611.1, C612.1, FB602.2, R605.1, TP606.1, U602.4 (VIN)
+VBAT_SAFE: C601.1, C609.1, FB601.1, FB602.1, TP601.1, TP602.1, TP603.1; also elsewhere on the board
/Project Architecture/Power Generation - Buck Converter/BUCK_3V3_ENABLE: NT602.2, U603.3 (EN)
/Project Architecture/Power Generation - Buck Converter/BUCK_3V3_FB: NT604.2, U603.5 (FB)
/Project Architecture/Power Generation - Buck Converter/BUCK_3V3_PG: R611.2, U603.8 (PGOOD)
/Project Architecture/Power Generation - Buck Converter/BUCK_3V3_SW: L603.1, U603.7 (SW)
/Project Architecture/Power Generation - Buck Converter/BUCK_5V_BOOT: C606.1, U601.6 (BOOT)
/Project Architecture/Power Generation - Buck Converter/BUCK_5V_ENABLE: R601.2, R602.1, U601.3 (EN/UVLO)
/Project Architecture/Power Generation - Buck Converter/BUCK_5V_FB: NT601.1, U601.8 (FB)
/Project Architecture/Power Generation - Buck Converter/BUCK_5V_MODE: R603.1, U601.1 (SYNC/MODE)
/Project Architecture/Power Generation - Buck Converter/BUCK_5V_PG: R604.2, U601.2 (PGOOD)
/Project Architecture/Power Generation - Buck Converter/BUCK_5V_SW: C606.2, L601.1, U601.5 (SW)
/Project Architecture/Power Generation - Buck Converter/BUCK_5V_VCC: C605.1, U601.7 (VCC)
/Project Architecture/Power Generation - Buck Converter/BUCK_12V_BOOT: C614.1, U602.6 (BOOT)
/Project Architecture/Power Generation - Buck Converter/BUCK_12V_ENABLE: R605.2, R606.1, U602.3 (EN/UVLO)
/Project Architecture/Power Generation - Buck Converter/BUCK_12V_FB: R609.2, R610.1, U602.8 (FB)
/Project Architecture/Power Generation - Buck Converter/BUCK_12V_MODE: R607.1, U602.1 (SYNC/MODE)
/Project Architecture/Power Generation - Buck Converter/BUCK_12V_PG: R608.2, U602.2 (PGOOD)
/Project Architecture/Power Generation - Buck Converter/BUCK_12V_SW: C614.2, L602.1, U602.5 (SW)
/Project Architecture/Power Generation - Buck Converter/BUCK_12V_VCC: C613.1, U602.7 (VCC)
GND: C601.2, C602.2, C603.2, C604.2, C605.2, C607.2, C608.2, C609.2, C610.2, C611.2, C612.2, C613.2, C615.2, C616.2, C617.2, C618.2, C619.2, C620.2, C622.2, C623.2, NT604.1, R602.2, R603.2, R606.2, R607.2, R610.2, TP613.1, TP614.1, TP615.1, U601.9 (GND), U602.9 (GND), U603.1 (PGND), U603.4 (AGND), U603.9 (PAD); also elsewhere on the board
unnamed: NT603.2, U603.6 (VOS)

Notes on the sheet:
+12V - Fan Power +5V - Gate Driver, Led +3V3 - Digital 3V3
3.3V 500mA Buck Regulator (2.25 MHz)
Ground
Test Points
[${#}] Power Generation - Buck Converter
DESIGN NOTE: MODE = LOW - Auto mode.
LAYOUT NOTE: Minimize switching node loop areas.
Filtered Input Power Rails
LAYOUT NOTE: Route feedback traces away from switching node.
DESIGN NOTE: L = (VIN - VOUT) * VOUT / Fsw * k * VIN Computed with: VIN = 0V, k = 0,15, VOUT = 5V, IOUT = 600mA
12V 600mA Buck Regulator (2.1 MHz)
Battery
Power Rails
Voltage Regulators
5V 600mA Buck Regulator (2.1 MHz)

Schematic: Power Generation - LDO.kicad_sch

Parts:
C701: 2u2 16V X7R; C_0805_2012Metric; Manufacturer Part Number C0805C225K4RAC3123
C702, C703: 100n 25V X7R; C_0805_2012Metric; Manufacturer Part Number 08053C104KAZ2A
C704: 4u7 16V X7R; C_0805_2012Metric; Manufacturer Part Number C0805C475K4RAC7210
NT701: LDO_EN; NetTie-2_SMD_Pad0.5mm
TP701, TP702: +3V3A; TestPoint_Pad_1.0x1.0mm
TP703, TP704: GND; TestPoint_Pad_1.0x1.0mm
U701: LP2992; SOT-23-5; Manufacturer Part Number LP2992AILDX-3.3/NOPB

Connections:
+3V3A: C704.1, TP701.1, TP702.1, U701.5 (VOUT); also elsewhere on the board
+5V: C701.1, C702.1, NT701.1, U701.1 (VIN); also elsewhere on the board
/Project Architecture/Power Generation - LDO/LDO_BYPASS: C703.1, U701.4 (BYPASS)
/Project Architecture/Power Generation - LDO/LDO_EN: NT701.2, U701.3 (EN)
GND: C701.2, C702.2, C703.2, C704.2, TP703.1, TP704.1, U701.2 (GND); also elsewhere on the board

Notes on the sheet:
+3V3A - Analouge 3V3
Voltage Regulator
[${#}] Power Generation - LDO
Test Points
LAYOUT NOTE: Place all cpaacitors to relevant pin. Minimize loop inductance.
+3V3 250mA Linear Regulator
Power Rails
Ground

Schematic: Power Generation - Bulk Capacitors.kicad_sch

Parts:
C501, C502, C503, C504, C505, C506, C507, C508, C509, C510, C511, C512, C513, C514, C515, C516, C517, C518, C519, C520, C521, C522, C523, C524, C525, C526, C527, C528, C529, C530, C531, C532, C533, C534, C535, C536, C537, C538, C539, C540, C541, C542: 10u 100V X7R; C_1210_3225Metric; Manufacturer Part Number C3225X7R2A106K250AC

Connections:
+VBAT_SAFE: C501.1, C502.1, C503.1, C504.1, C505.1, C506.1, C507.1, C508.1, C509.1, C510.1, C511.1, C512.1, C513.1, C514.1, C515.1, C516.1, C517.1, C518.1, C519.1, C520.1, C521.1, C522.1, C523.1, C524.1, C525.1, C526.1, C527.1, C528.1, C529.1, C530.1, C531.1, C532.1, C533.1, C534.1, C535.1, C536.1, C537.1, C538.1, C539.1, C540.1, C541.1, C542.1; also elsewhere on the board
GND: C501.2, C502.2, C503.2, C504.2, C505.2, C506.2, C507.2, C508.2, C509.2, C510.2, C511.2, C512.2, C513.2, C514.2, C515.2, C516.2, C517.2, C518.2, C519.2, C520.2, C521.2, C522.2, C523.2, C524.2, C525.2, C526.2, C527.2, C528.2, C529.2, C530.2, C531.2, C532.2, C533.2, C534.2, C535.2, C536.2, C537.2, C538.2, C539.2, C540.2, C541.2, C542.2; also elsewhere on the board

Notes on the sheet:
DESIGN NOTE: An external precharge ciruit is advised to charge bulk capacitors. If multiple boards are connected.
Bulk Capacitors 14 x 4.7 = 197.4 uF
[${#}] Power Generation - Bulk Capacitors

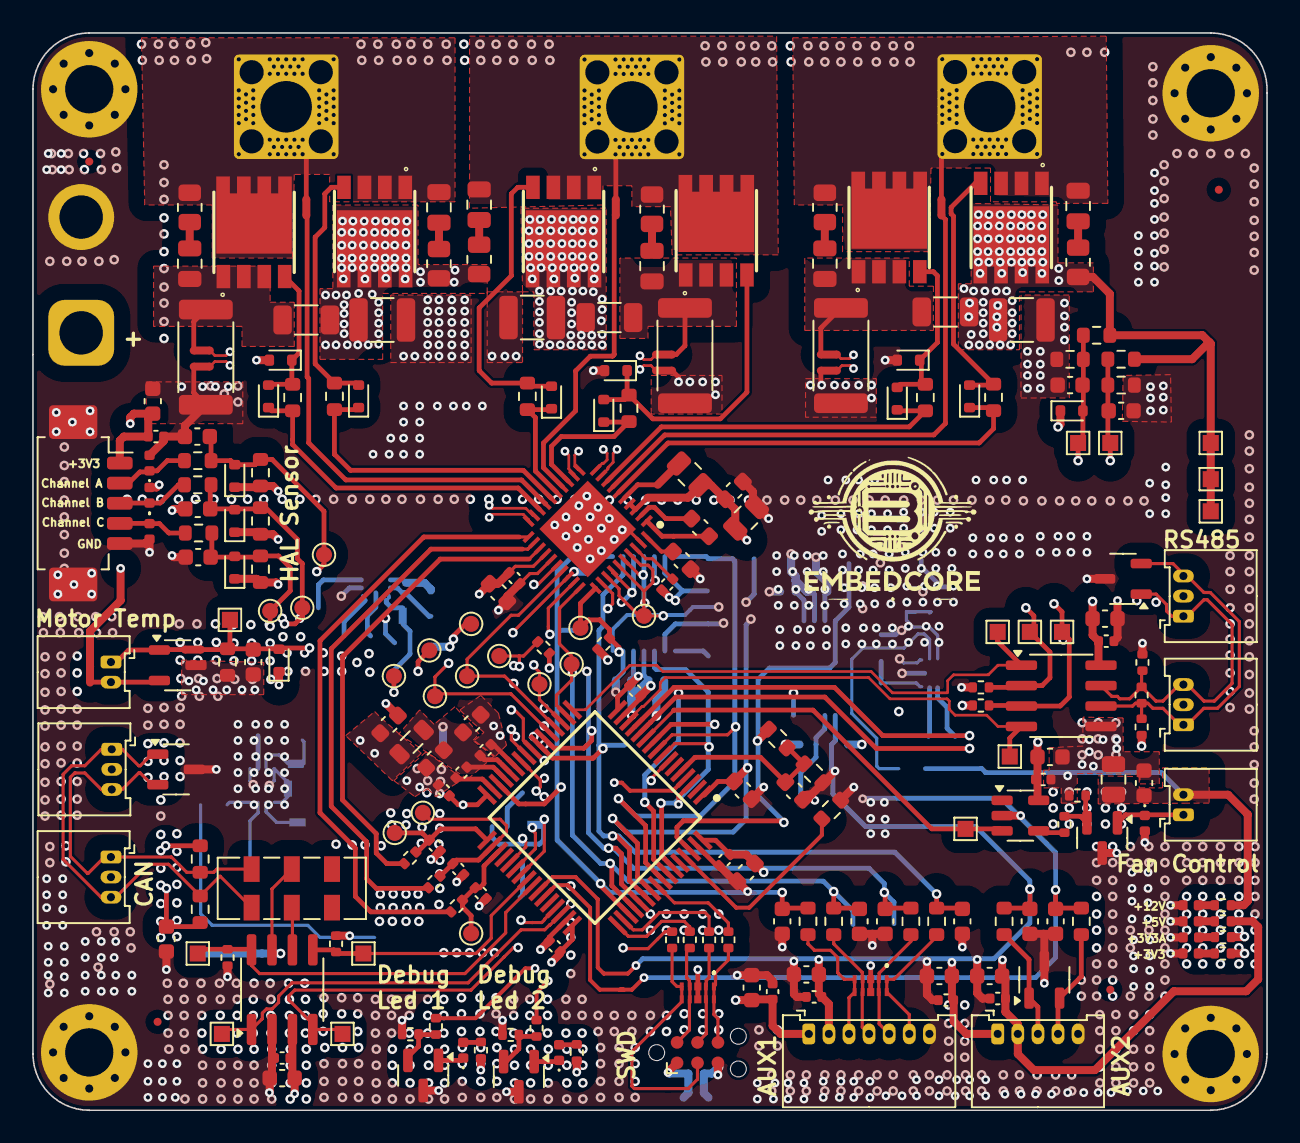
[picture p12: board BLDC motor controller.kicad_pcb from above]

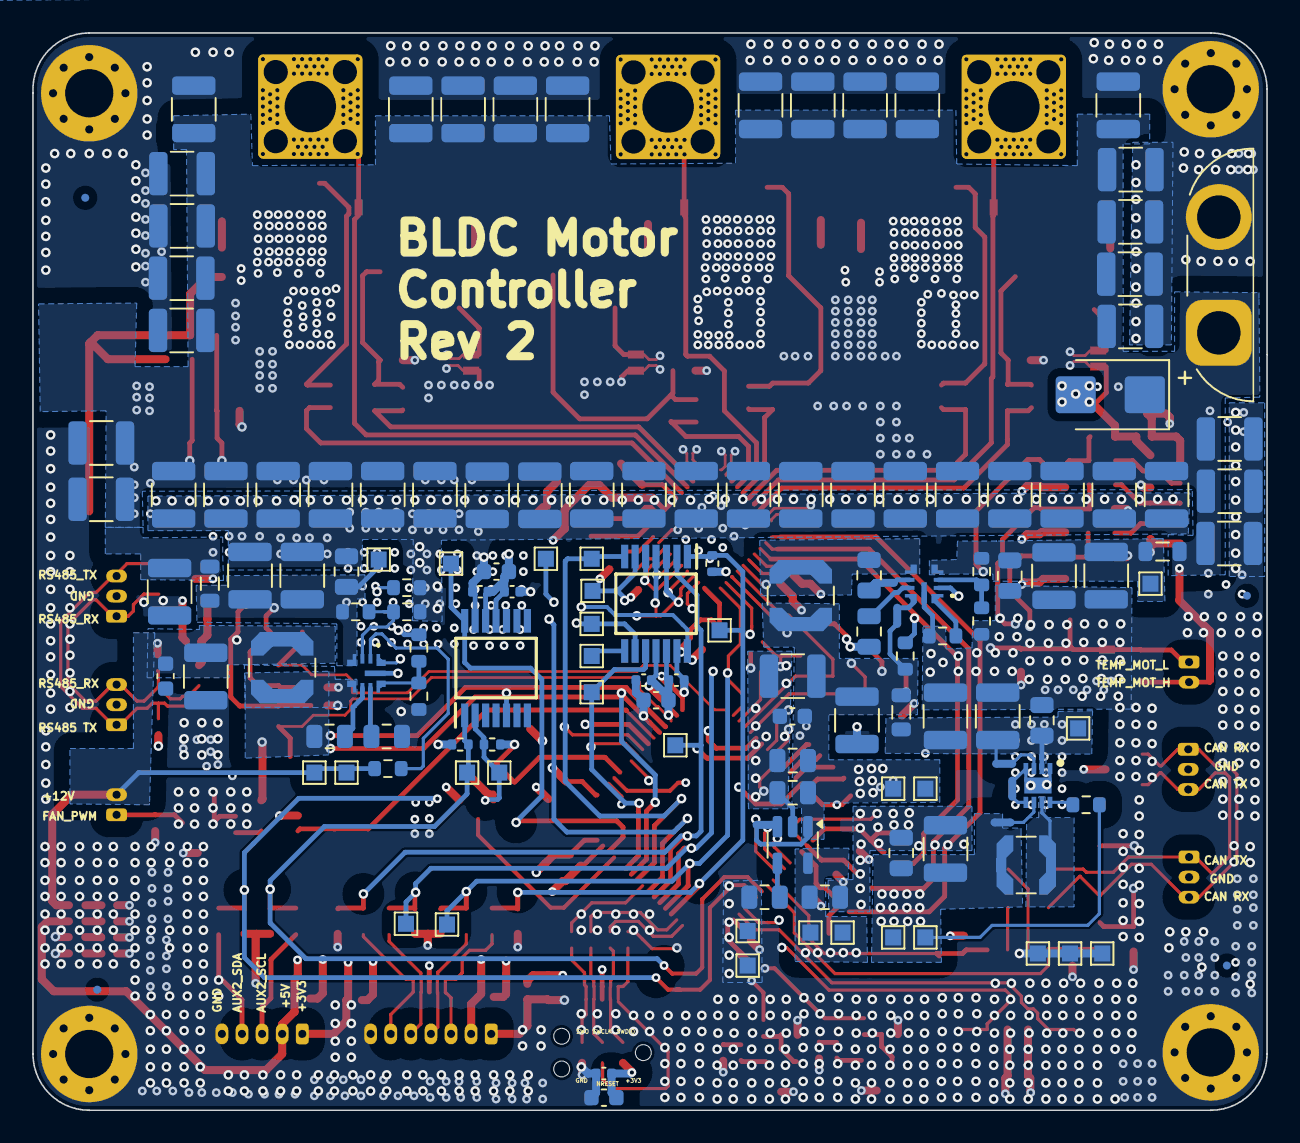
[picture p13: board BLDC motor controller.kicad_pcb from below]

Board: 6 copper layers, 76.8 x 67.0 mm, 382 parts (142 on the bottom side), 156 nets.
